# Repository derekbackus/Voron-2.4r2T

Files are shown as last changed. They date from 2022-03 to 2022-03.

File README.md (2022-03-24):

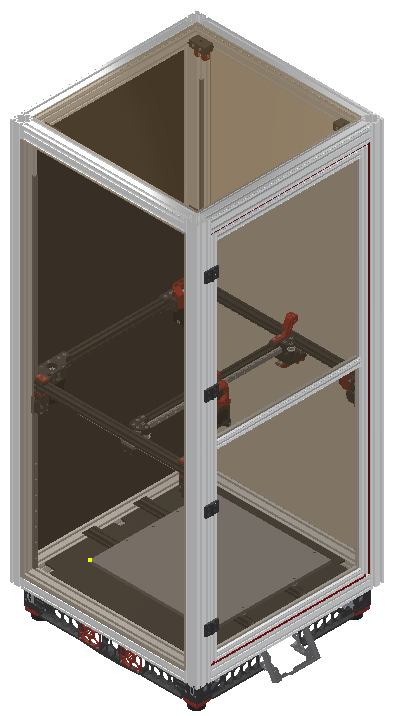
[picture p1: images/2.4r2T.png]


# Voron-2.4r2T
- 350X x 350Y x 920Z Voron 2.4r2 Tall.
- Basically the 2.4r2T is a Voron 2.4r2 with 4040 extrusions that has a Z travel of 920mm. 

Here's a 3D view of the printer. Unfortunately, Autodesk expires this every 30 days. If it's expired, let me know and I'll re-upload it.
[3D CAD View](https://autode.sk/3Ix8QP8) - Expires 4/22/2022

# Why Build this Monster?
At my model shop [KiwiMill](https://www.kiwimill.com) we like to print a lot of tall objects -- boat hulls, display models etc. and instead of printing them in multiple 350mm tall pieces, I wanted to build a printer that could do this in one or two pieces. This is a production machine so I'm not trying to save on costs or skimp on anything. I chose 4040 because it was strong, easy to work with, rigid and, most importantly, fully compatible with the existing Voron 2.4r2 parts made for 2020 extrusions.
# Design Objectives
- Make a printer that reuses most, if not all of the standard Voron parts, but is as tall as possible. The machine should hold up to 24hr/day use and be as easy as possible to maintain and use. Just like the Voron 2.4r2, it should be able to easily print ABS as well as PLA and other materials that can be printed on a Voron. The chamber needs to have filters to clean the air to keep the VOCs out of the work area.
# Current Issues
- The bowden tube to the toolhead is so long it gets stuck on things and curles into the wrong places. I removed the tube and just have the raw filament going into the toolhead -- this works great, but I need to make some kind of guide for the top so it looks nice.
# Videos
I've made some videos to demonstrate how to do some of the more complicated things in this build.
- [Tapping 4040 Extrusion for Blind Joints](https://youtu.be/ohi948kkzv4)
- [Drilling Clearance Holes in 4040 Extrusion for Blind Joings](https://youtu.be/enlHb-844ug)
# Notes & Design Choices
- 1000mm MGN9 rails were easy to get, so I used those for the Z rails. This makes the maximum print height about 920mm.
- A 350X x 350Y Voron design will be used as parts are readily available including built plates, heaters, gantry rails, etc.
- Coroplast will be used on the back and bottom -- laser cut to size. Or maybe ACM. We've got a local supplier of ACM sheet and I've got a 4K laser cutter, so this may be a fun side project.
- The bottom panels and top panel are unchanged from the 2.4r2.
- 4040 rails will be used on the entire frame.
- 2020 rails will be used on the single door.
- Clear anodized extrusions are about 1/2 the price so I used those.
- Extrusions will be ordered without machining -- Misumi has a month lead time on machining AND you can do it yourself with the ez drill jig I designd, a 1/4" drill bit and a 5mm tap.
- I'm trying to figure out how to heat this chamber -- it's so huge. Ideas are: 1) add a plate above the gantry that moves with the gantry, keeping the heat in the bottom of the printer, 2) add a second built plate & heater, controlled exactly like the bed somewhere in the chamber.
# Coverting from an Existing Voron 2.4
- If you have a Voron 2.4, upgrade to all the 2.4r2 parts while you are doing this project. I just printed everything and re-built the whole thing down to the last bolt.
- Follow the steps below for Converting from an Existing Voron 2.4r2
# Converting from an Existing Voron 2.4r2
- The gantry will be used, unchanged
- The gantry wiring and XY endstop pod wiring will need to be re-run because it is longer.
- You'll need a longer Z drag chain.
- 4040 extrusions are used on the entire frame for rigidity.
- 2020 extrusions are used on the door.
- Longer Z belts.
- You may want a new hot end so you can use bigger nozzles, faster. I chose the Rapido.
- New custom panels (back, sides, door)
# BOM (only the changes from a 2.4r2 are listed)
- Qty 1: Z chain -- I like the cheap, generic ones. [Amazon Link](https://www.amazon.com/gp/product/B08R1M9J2H/ref=ppx_yo_dt_b_asin_title_o02_s00?ie=UTF8&th=1)
- Qty 4: 1M MGN9 Rails & Pillow Blocks [Robodigg MGN9-2H-1000](https://www.robotdigg.com/product/347/Custom-length-GCr15-MGN9,-MGN12-or-MGN15-Linear-Rail-n-Carriage)
- Qty 4: Misumi 1180mm 4040 Extrusion [Misumi Link](https://us.misumi-ec.com/vona2/detail/110302684530/?HissuCode=HFS5-4040-1180). Please note: you will need to drill your own clearance holes for the hex key. This is easy with a 1/4" drill bit and the guide in the STL folder.
- Qty 8: Misumi HFS5-4040-470 470mm 4040 Extrusion (I use clear anodized because it is MUCH cheaper, black works too) [Misumi Link](https://us.misumi-ec.com/vona2/detail/110302684530/?HissuCode=HFS5-4040-470). Plesae note: You will have to tap all the holes in this extrusion with an M5 tap. Use a pistol drill, tapping fluid and a new, sharp tap. Clamp the extrusion to a table because it likes to spin in you hand. This is easy, but be very careful -- you can break a tap. If you do break a tap, just break it off flat -- there are THREE other screws in each extursion to hold it -- which is plenty.
- Qty 2: Misumi 1088mm 2020 Extrusion HFS5-2020-1088 [Misumi Link](https://us.misumi-ec.com/vona2/detail/110302683830/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) - vertical door extrusions - Please note: you will need to drill your own clearance holes for the hex key. This is easy with a 1/4" drill bit and the guide in the STL folder.
- Qty 3: Misumi 424mm 2020 Extrusion HFS5-2020-424 [Misumi Link](https://us.misumi-ec.com/vona2/detail/110302683830/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) - horizontal door extrusions - Plesae note: You will have to tap all the holes in this extrusion with an M5 tap. Use a pistol drill, tapping fluid and a new, sharp tap. Clamp the extrusion to a table because it likes to spin in you hand. This is easy, but be very careful -- you can break a tap and, if you do, you're fucked.
- Qty 10 Meters: 9mm Gates Belt [Fabreeko](https://www.fabreeko.com/products/gates-gt2-open-belt-ll-2gt-6-9-12-reinforced?variant=42466462761215)
- Qty 2: Side panels
- Qty 2: Door panels
- Qty 1: Back panel
- Qty 4: 2020 hinges & handles [Amazon Link](https://amazon.com/gp/product/B07NQ5WHW9/ref=ppx_yo_dt_b_asin_title_o00_s00?ie=UTF8&psc=1)
- Lots and Lots: 20ga PTFE Wire [Remington Industries](https://www.remingtonindustries.com/)
- Shit-ton of 3mm weather seal.
# stl Files to Print
- 2020_Drill_Jig - Use this to drill the clearance holes in the 2020 on your door.
- 4040_Drill_Jig - Use this to drill the clearance holes in your 4040 vertical pieces.
- Filtered_Inliet_Skirt - Removes the switch hole from the stock rear skirt.
- Switch_Skirt - Moves the switch to the right, front.
- MGN9_4040_Rail_Guide - Guide to align your MGN9 rails on the 4040 extrusion.
- Panel_Mount - OPTIONAL - PITFT50 mount for the 4040 extrusion. Use this repo for the PITFT50 frame and my mount for the 4040 extrusion if you want to mount it to the front. You can also use the mount linked in the PITFT50 repo for undermount. [PITFT Frame](https://github.com/VoronDesign/VoronUsers/tree/master/printer_mods/alanho/BTT_PITFT50_v2_Mount)
- Foot_Spacer - Goes between the foot and the mount to rais the printer up slightly so the screen doesn't sit on the desktop.
# CAD Files
- Panels are in the DXF folder. You can use these to get custom laser-cut panels or cut them youself. I use coroplast for the back and bottom panels and polycarbonate for the top, sides and front panels.
- A STEP file is in the CAD folder so you can see how things go together.
# Mods (optional)
- Klicky [Klicky Github](https://github.com/jlas1/Klicky-Probe)
- Sexbolt Z Endstop [kb-3d.com Link](https://kb-3d.com/store/voron/301-hartk-sexbolt-z-endstop-mod-for-voron-v2-hardware-kit-1634072159749.html)
- LED Enclosure Lights [Voron Github](https://github.com/VoronDesign/VoronUsers/tree/master/printer_mods/DerekBackus/LED_Holder)
- PITFT50 LCD [kb-3d.com Link](https://kb-3d.com/store/controllers-displays-drivers/419-btt-pitft50-v20-5-inch-pi-lcd-touchscreen-display-1639871340640.html)
- Qty 2. Nevermore filters [Nevermore Github](https://github.com/nevermore3d/Nevermore_Micro)
- 4 Z Rail Stops from the Trident Repo to prevent the Z pillow blocks from coming off the MGN9 rails. Trident/STLs/Z_Assembly/[a]_z_rail_stop_x3.stl
- Extrusion backers. [Fabreeko](https://www.fabreeko.com/products/v2-4-trident-titanium-extrusion-backers?variant=40722088034502)

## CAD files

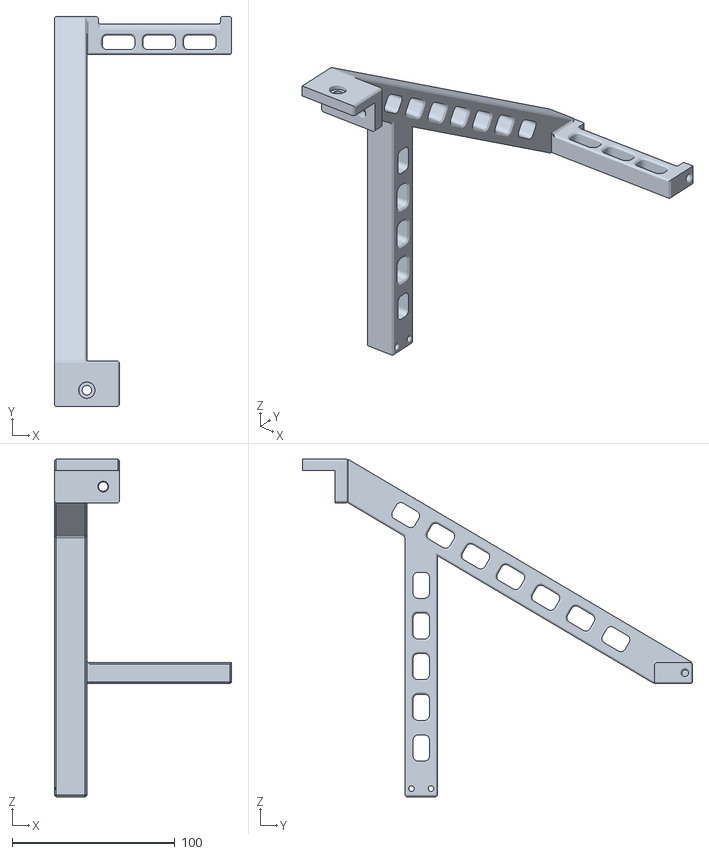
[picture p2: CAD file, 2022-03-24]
stl/Spool Holder.stl
109.0 x 239.7 x 207.5

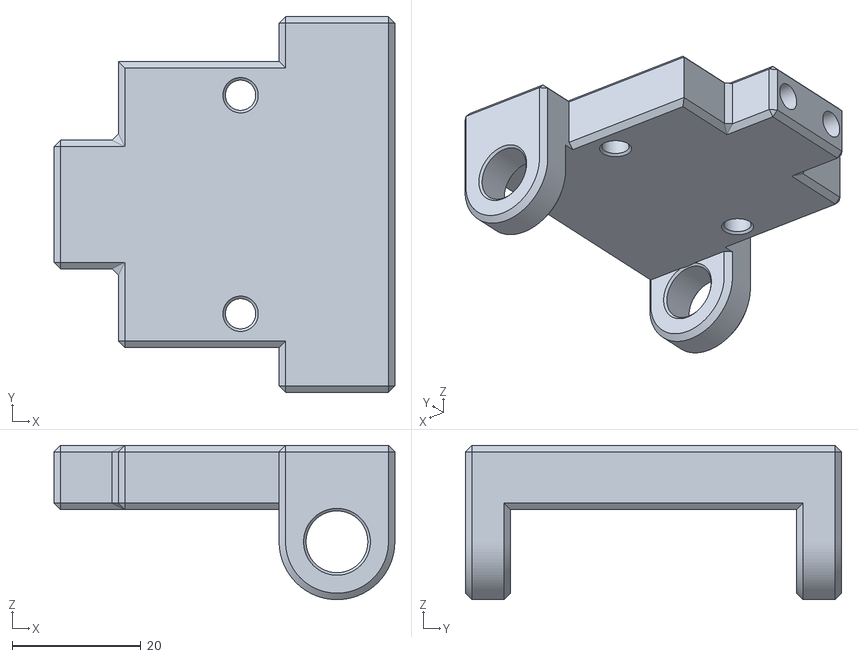
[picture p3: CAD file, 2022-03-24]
stl/Spool Holder Filament Holder.stl
53.0 x 58.5 x 24.0

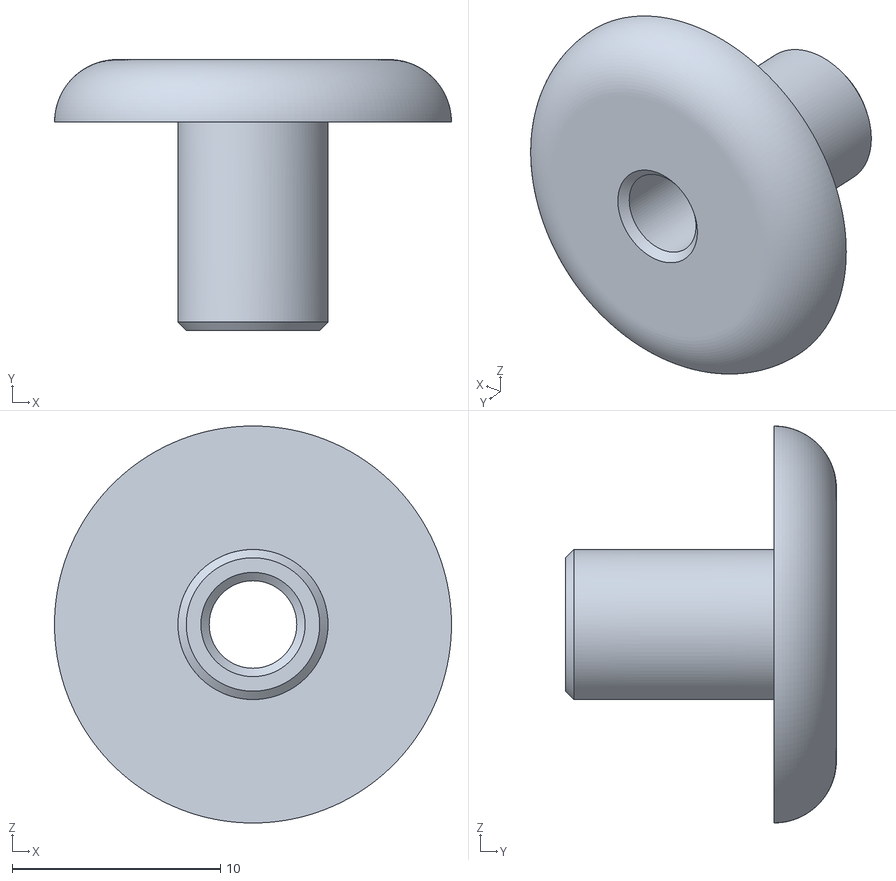
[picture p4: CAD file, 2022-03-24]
stl/Bowden_Nipple.stl
19.0 x 13.0 x 19.0

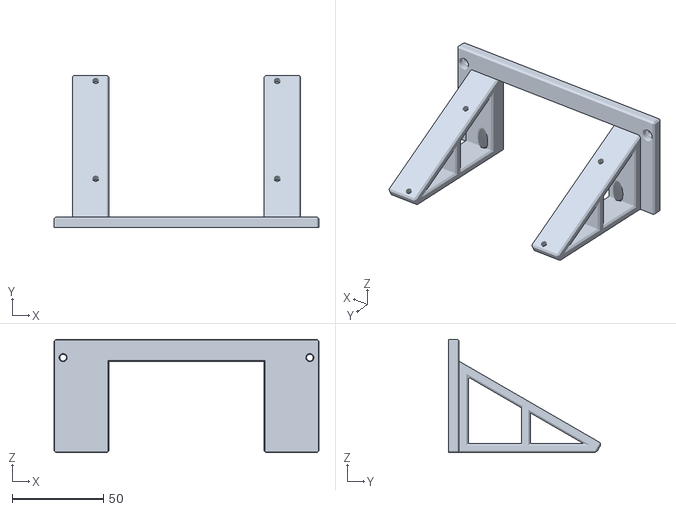
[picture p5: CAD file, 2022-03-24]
stl/Panel Mount Top v2.stl
145.0 x 83.4 x 62.0

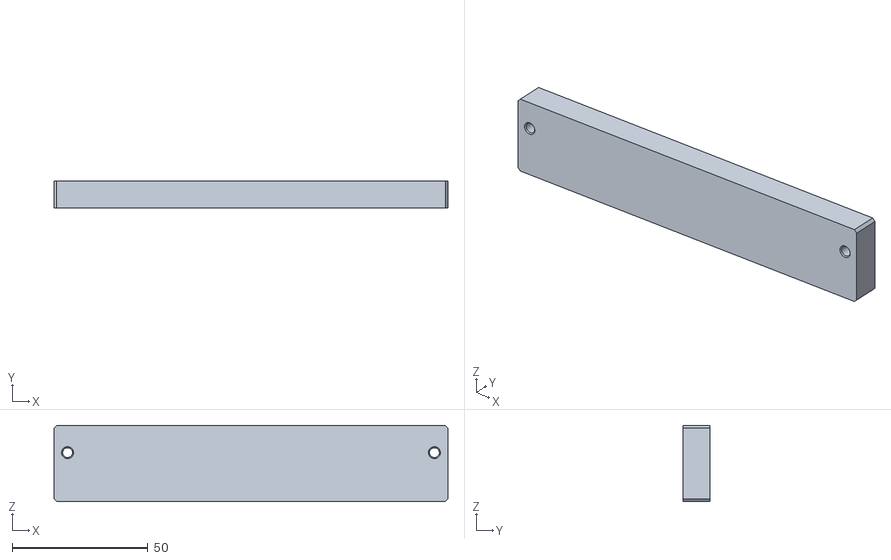
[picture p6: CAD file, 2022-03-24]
stl/Panel Mount Spacer.stl
145.0 x 10.0 x 28.0

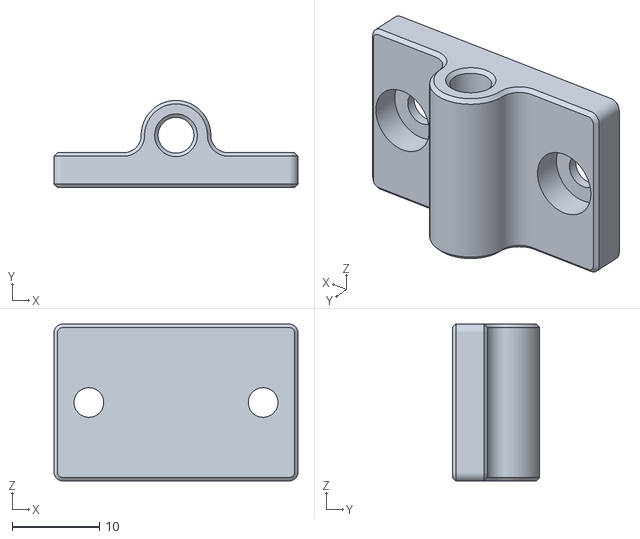
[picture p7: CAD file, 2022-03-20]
stl/Bowden_Guide.dwg.stl
28.0 x 10.0 x 18.0

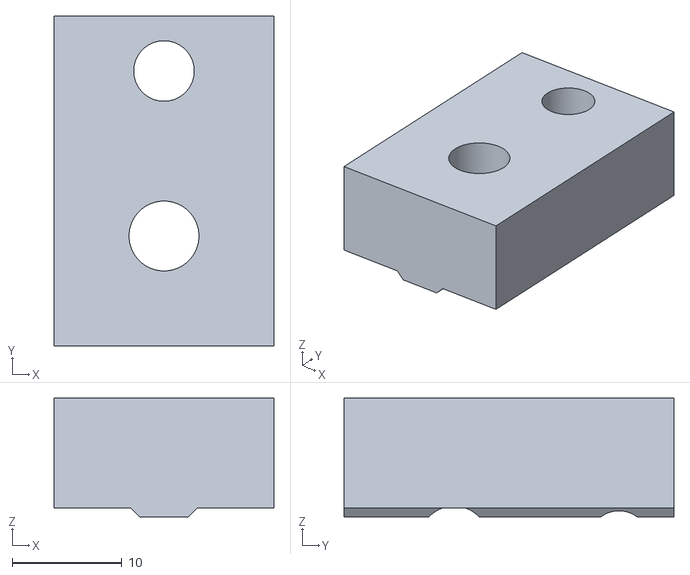
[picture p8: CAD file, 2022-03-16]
stl/2020_Drill_Jig.stl
20.0 x 30.0 x 10.8

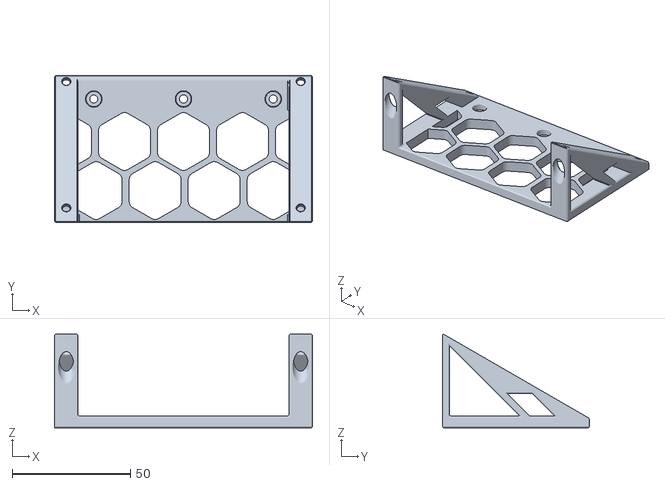
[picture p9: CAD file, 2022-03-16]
stl/Panel_Mount.stl
109.3 x 62.4 x 39.8

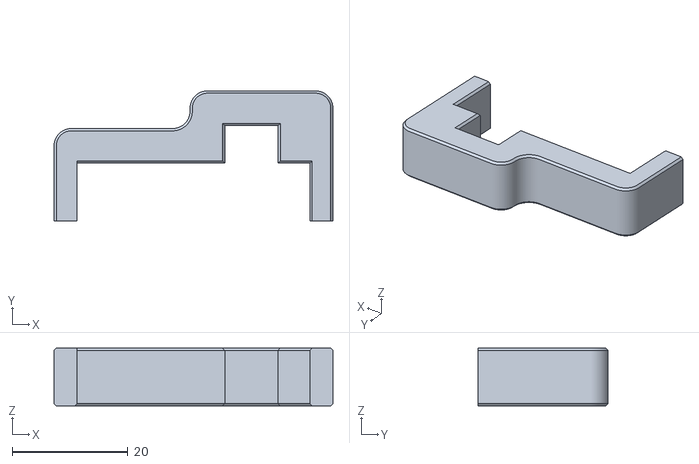
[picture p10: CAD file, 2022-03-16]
stl/MGN9_4040_Rail_Guide.stl
48.2 x 22.5 x 10.0

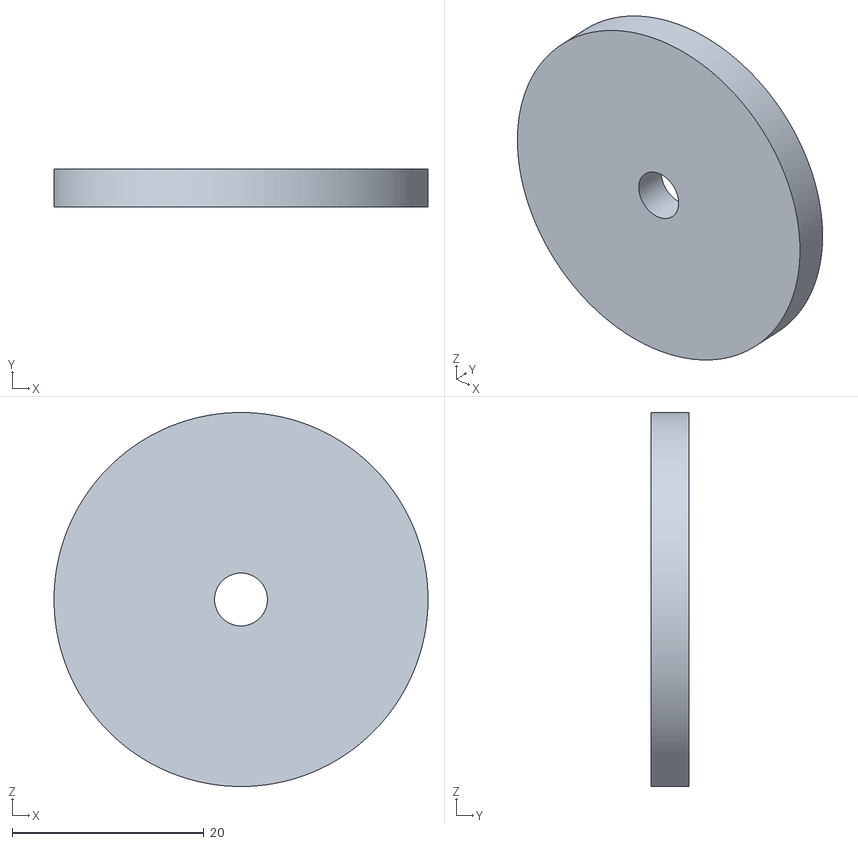
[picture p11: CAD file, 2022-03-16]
stl/Foot_Spacer.stl
39.0 x 4.00 x 39.0

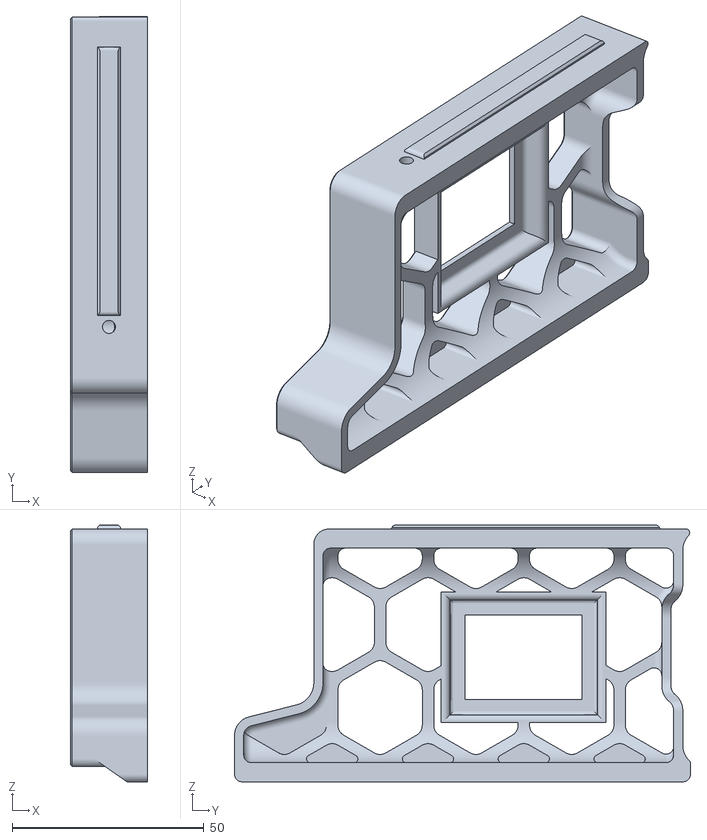
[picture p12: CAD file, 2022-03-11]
stl/Switch_Skirt.stl
20.0 x 119.0 x 67.0

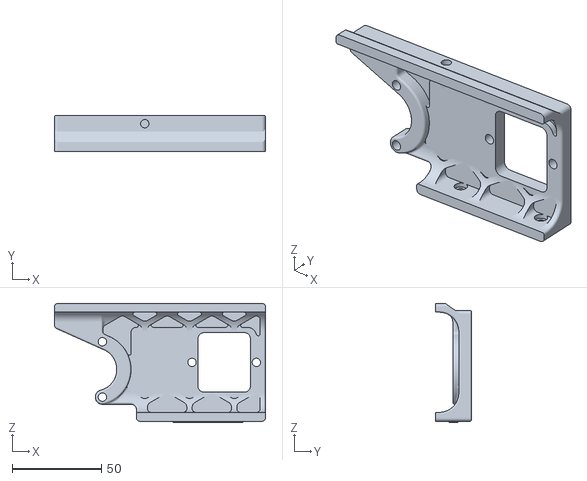
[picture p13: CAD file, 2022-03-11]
stl/Filtered_Inlet_Skirt.stl
118.0 x 20.0 x 66.8

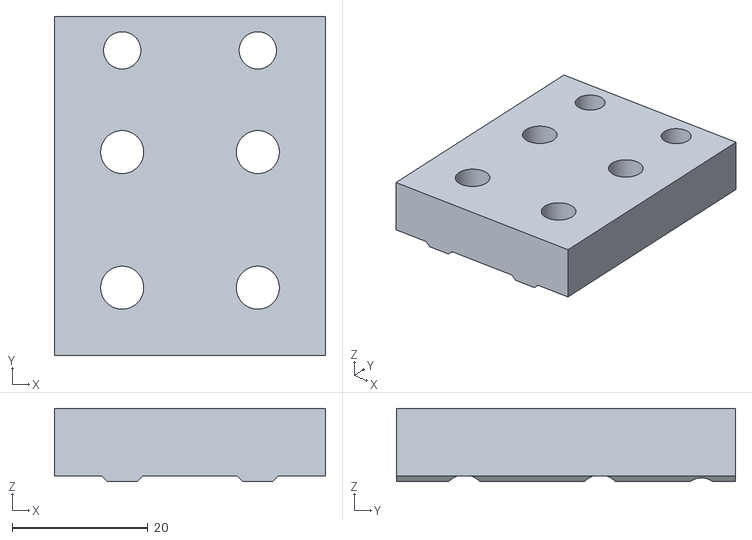
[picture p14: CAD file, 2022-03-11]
stl/4040_Drill_Jig.stl
40.0 x 50.0 x 10.8

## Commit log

2022-03-11 Updated Solid & STP files
    [4040 Drill Jig.stl, Filtered_Inlet_Skirt.stl, Switch Skirt.dwg.stl]
2022-03-12 Create Voron 2.4r2 Tall STEP Assembly.zip
2022-03-15 Rename Skirt
    [Switch Skirt.stl]
2022-03-16 Add STL files
    [2020_Drill_Jig.stl, 4040_Drill_Jig.stl, MGN9_4040_Rail_Guide.stl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]
2022-03-16 Add Foot Spacer
    [Foot_Spacer.stl, MGN9 4040 Rail Guide.stl]
2022-03-16 Rename Guide
    [MGN9 4040 Rail Guide.stl]
2022-03-22 Updated CAD Link
2022-03-24 Add panel mount and spool holder
    [Bowden_Nipple.stl, Panel Mount Spacer.stl, Panel Mount Top v2.stl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]
